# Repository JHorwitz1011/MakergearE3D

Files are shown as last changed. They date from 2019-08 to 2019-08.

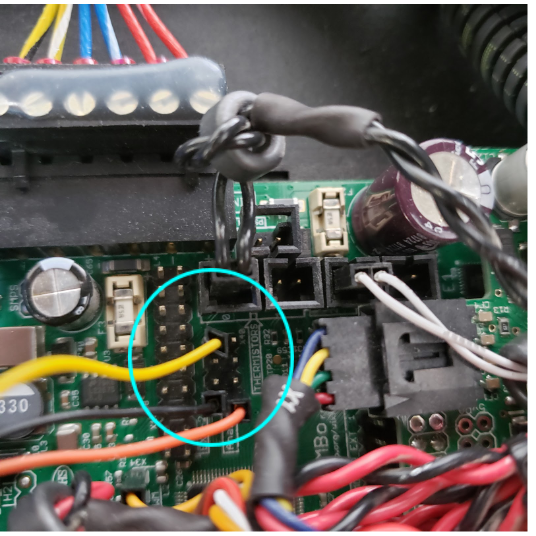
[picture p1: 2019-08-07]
Analog Pins.PNG

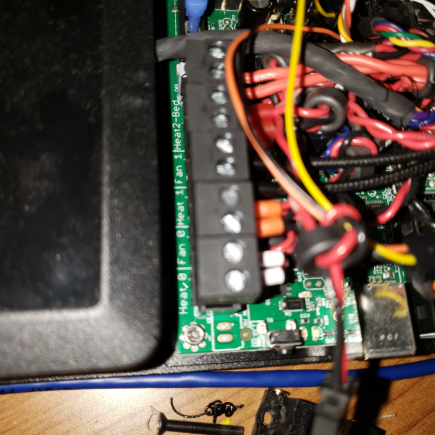
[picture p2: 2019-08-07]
Heater Pins.PNG

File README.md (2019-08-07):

# MakergearE3D

This project was creted by Jim Horwitz, an intern at MakerGear.  

Objectives  
 -- High temperature upgrade kit  
 -- E3D upgrade kit  

**Components**

Heater - https://e3d-online.com/high-temperature-heater-cartridges  
65W @ 24V  
RAMBo 1.3 MOSFETs can handle  
Rated at 117W, 89A  
Connector of heater is not compatible with the port on M3, potential mod?  
Solution: Remove the old heater block wires from the screw terminal and replace with the 65W heater wires.  
Zip tie through the back to the filament drive   

Heat Break - https://e3d-online.com/v6-titanium-heat-break-1-75mm  
Lower heat conductivity  
Maybe not necessary - requires further testing  
Alternative: https://e3d-online.com/v6-heat-break  
Plated Copper Heater Block - https://e3d-online.com/v6-plated-copper-heater-block  
Aluminum heater blocks will soften at high temperatures  

High Temp PTFE tubing - https://e3d-online.com/capricorn-bowden-tubing-100mm  
For heat sink  
Normal PTFE will melt with high temp. Materials such as PEEK  

PT100 Temperature Sensor - https://e3d-online.com/pt100-temperature-sensor  
Accurately reads temperatures up to 400 deg. C  
Alternative: https://e3d-online.com/type-k-thermocouple-cartridge  
Requires a different amplifier board  
  
PT100 Amplifier Board - https://e3d-online.com/pt100-amplifier-board  
Required for the PT100 Temperature Sensor to work  
Requires Vcc and GND pins from RAMBo 1.3  
Signal pin must be connected to analog input of RAMBo 1.3  
Explained later  

Threaded Heat Sink - https://e3d-online.com/v6-threaded-heatsink  
Alternative groove mount: https://e3d-online.com/v6-heatsink-1-75mm-universal  

**Firmware Changes** -  attached in Marlin firmware

Configuration.h

temperature sensor 1 changed to match signal from PT100 amplifier board.   

pins_RAMBO.h

temp sensor 1 pin changed to match signal pin on analog pins input.  

**Hardware Changes**

Refer to Analog pins.png

        Blue circle - Analog Pins location on RAMBo 1.3 Board

        Yellow Wire - Signal wire of PT100 Amplifier Board to corresponding analog pin 5 in firmware (shown above)
        Black Wire - GND of Amplifier Board
        Orange Wire - Vcc of Amplifier Board

Refer to Heater Pins.png 

        Heater 1 Screw Terminal - replaced with E3D Heater Cartridge wires (glossy black in the picture above)
        Third terminal from the bottom

**GCode Changes**
http://marlinfw.org/meta/gcode/  
These changes save to the EEPROM of the RAMBo board, and are not changed when updating the firmware of the board.  

Offset between nozzle - M218 command  
T1 specifies extruder head, X/Y/Z specifies axis.  
For vertical adjustments, use Z.  
-33.26 worked with an M3 with a normal T0, and a modded T1 with Ryan’s 3D printed mount  
Negative values move the bed further from the hotend (down).  

Printout from M503  

        M218 T1 X252.00 Y0.00 Z-33.26
  
http://marlinfw.org/docs/gcode/M218.html  

Autotune PID - M303  

        M303 E1 S265 C10 

This will run 10 cycles of PID autotuning based on 265 deg. C.  
Copy the PID settings into M301, using P, I, and D before each number to change their respective values.  

Printout from M503  

        M301 P15.33 I1.39 D42.38 C120.00 L20

http://marlinfw.org/docs/gcode/M303.html  
http://marlinfw.org/docs/gcode/M301.html

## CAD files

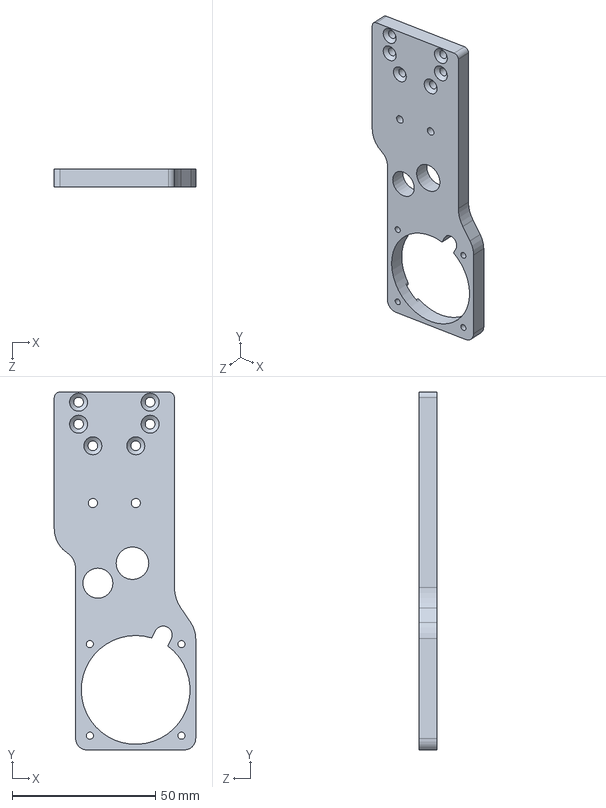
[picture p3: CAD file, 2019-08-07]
HotendMountingPlate_2516-1_REV_3.1.SLDPRT
49.5 x 125.1 x 6.35 mm

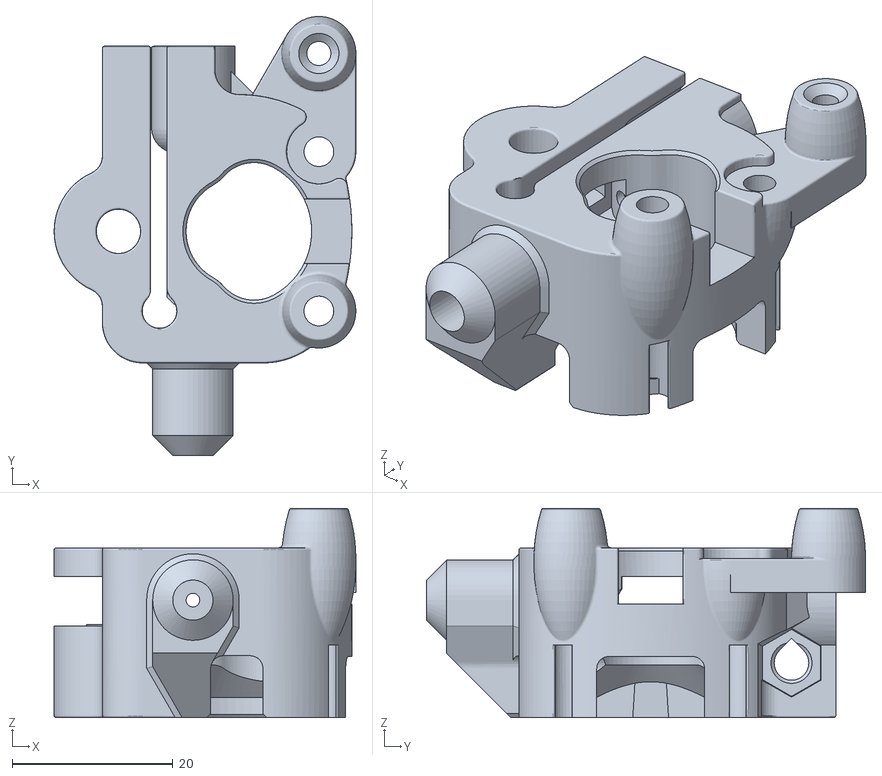
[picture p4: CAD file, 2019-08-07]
M3FilamentDrive_8-7-19 v2.stl
37.5 x 54.5 x 26.0

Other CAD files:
HotendMountingPlate_2516-1_REV_3_7-26-19 v3.step

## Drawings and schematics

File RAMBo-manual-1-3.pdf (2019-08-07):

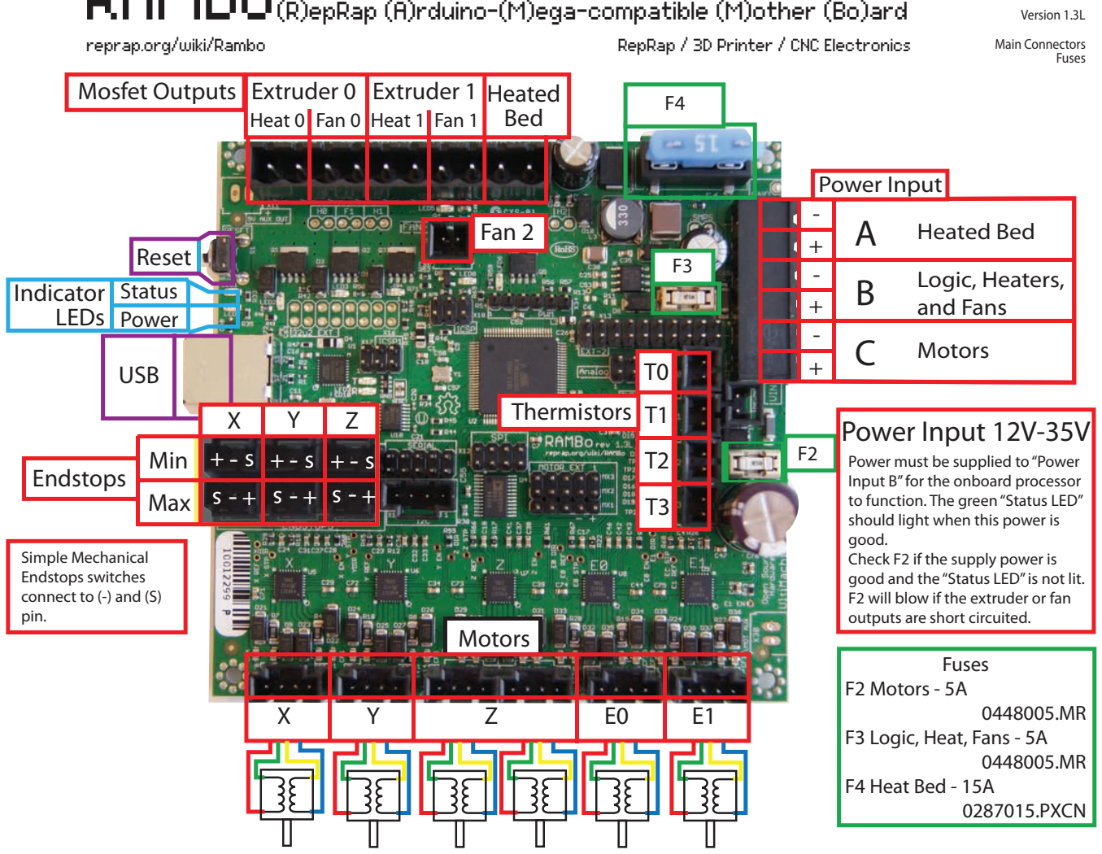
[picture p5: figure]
Fuses F2 Motors - 5A; 0448005.MR F3 Logic, Heat, Fans - 5A 0448005.MR F4 Heat Bed - 15A 0287015.PXCN; Fuses; Indicator LEDs; Status Power; Reset; USB; A Heated Bed; C Motors; Logic, Heaters, B and Fans; Power Input; Power must be supplied to “Power Input B” for the onboard processor to function. The green “Status LED” should light when this power is good. Check F2 if the supply power is good and the “Status LED” is not lit. F2 will blow if the extruder or fan outputs are short circuited.; Power Input 12V-35V; Mosfet Outputs; Extruder 0; Extruder 1; Fan 2; Heated; Heat 0; Fan 0; Heat 1; Fan 1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

Open Source Hardware | Copyright 2014 - UltiMachine -Johnny,Britt,Dorothy,Lee, Bruce

Handle with care. Static Sensitive device.

Test all electronics thoroughly before placing into service.

# Do not leave power supplied to electronics unattended, or run machines

# This is NOT a toy and it contains small and sharp parts. Children can choke or

never leave printer/parts unattended.

reprap.org/wiki/Rambo | RepRap / 3D Printer / CNC Electronics

## RAMBo(R)epRap (A)rduino-(M)ega-compatible (M)other (Bo)ard

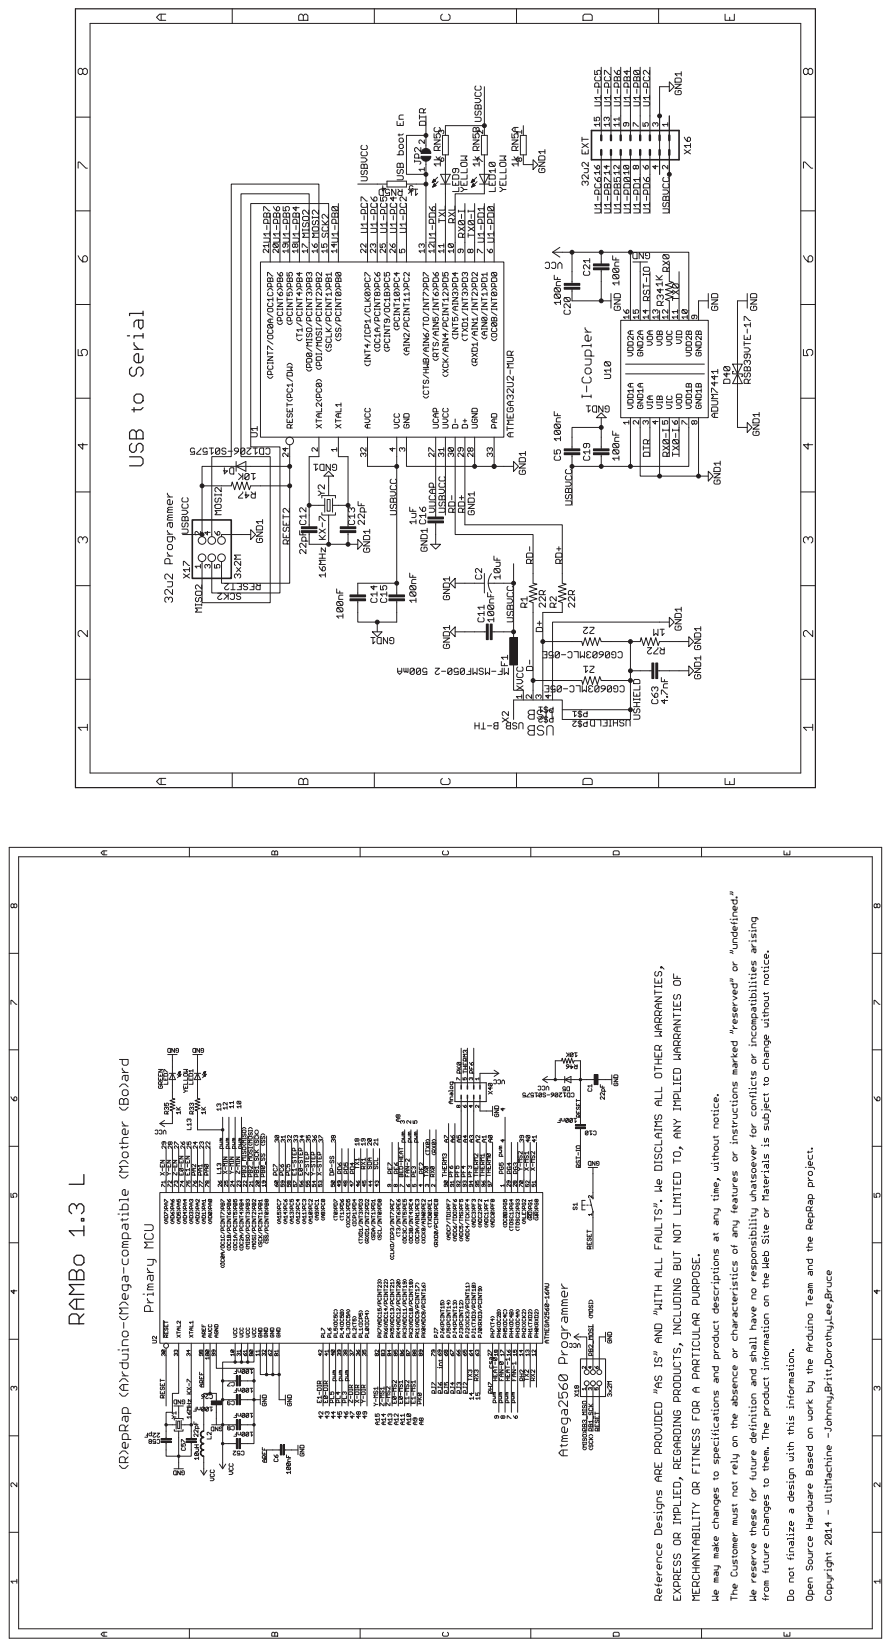
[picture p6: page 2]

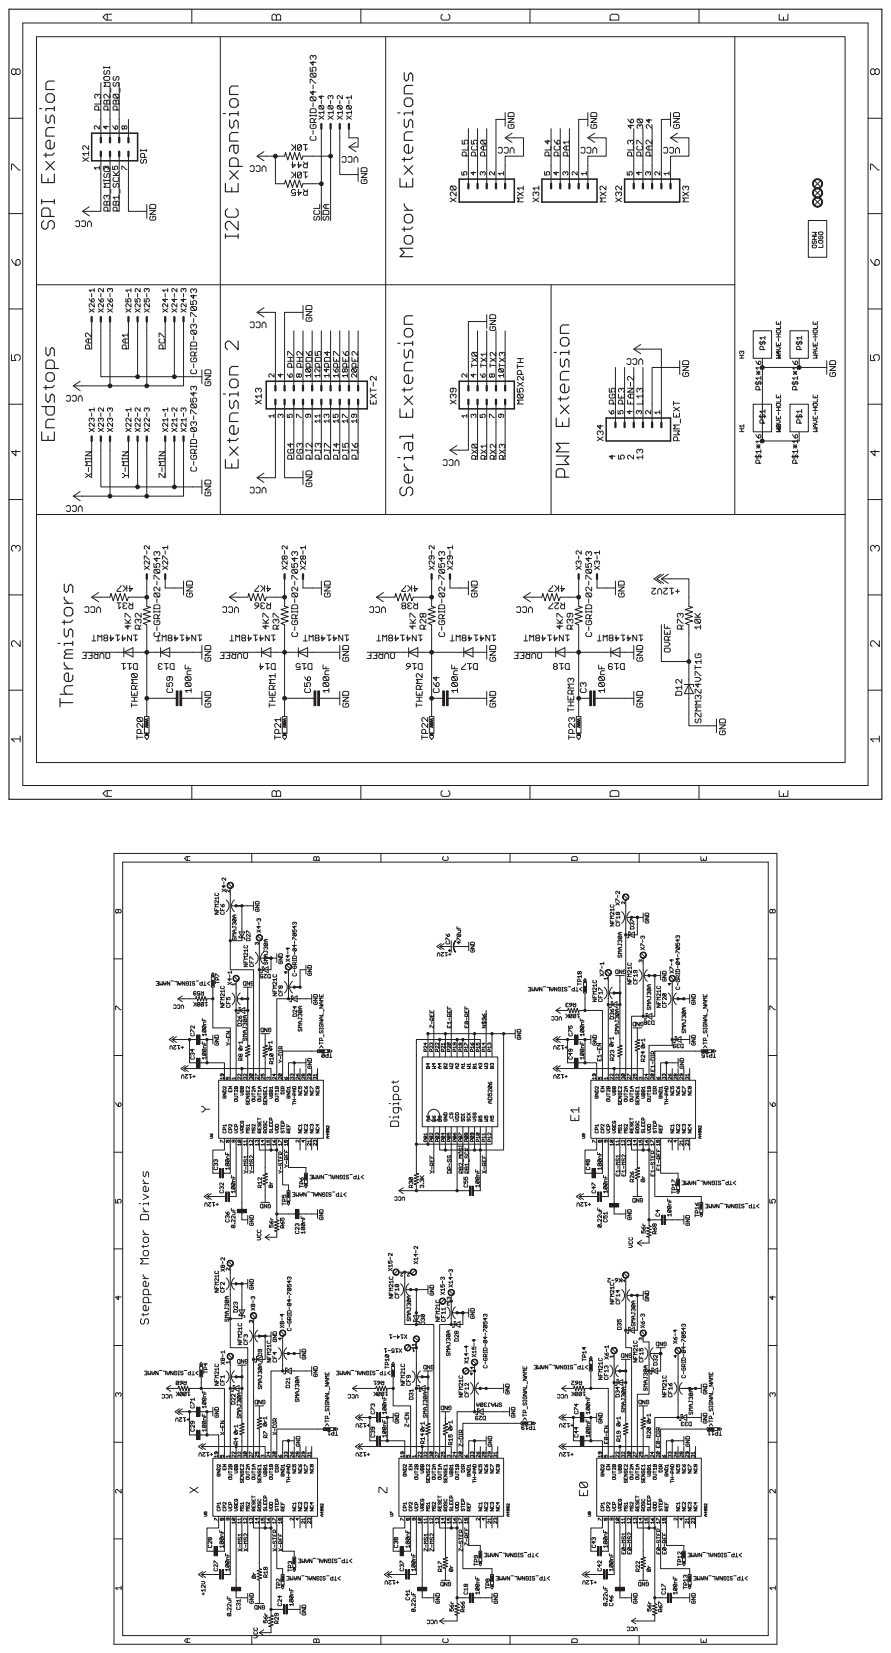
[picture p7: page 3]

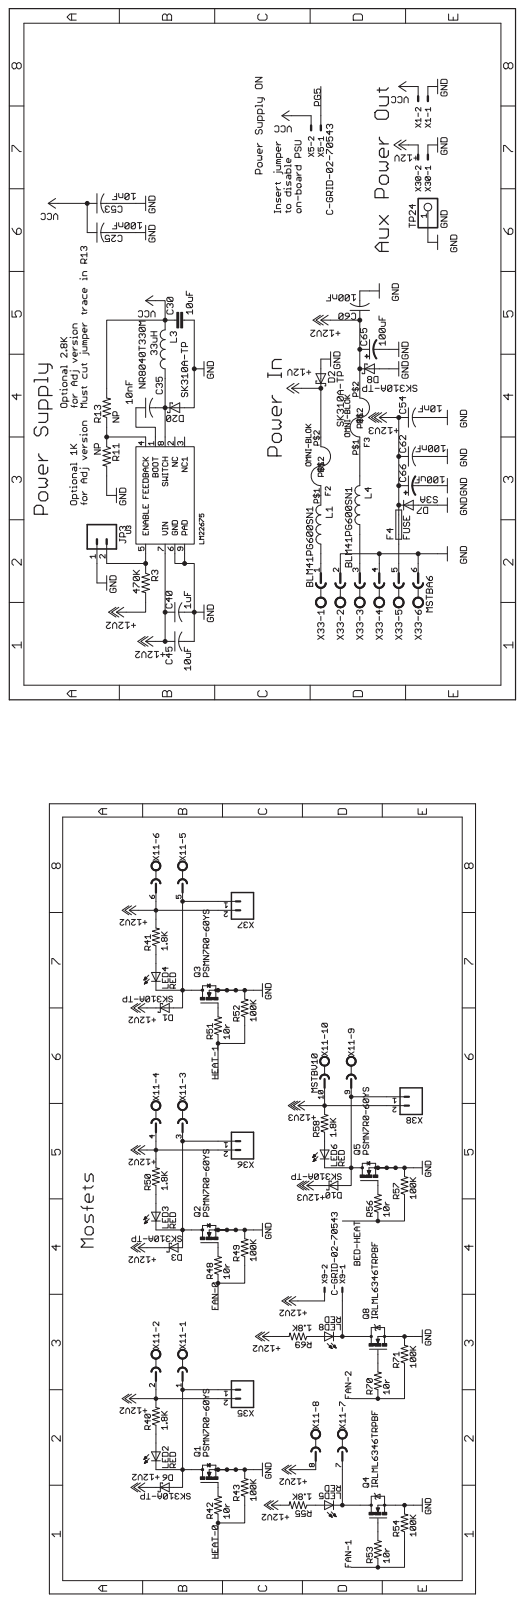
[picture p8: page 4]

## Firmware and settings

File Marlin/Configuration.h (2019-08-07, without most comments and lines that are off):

#define CONFIGURATION_H
#define CONFIGURATION_H_VERSION 010100
#define STRING_CONFIG_H_AUTHOR MAKERGEAR_AUTHOR // Who made the changes.
#define SHOW_BOOTSCREEN
#define STRING_SPLASH_LINE1 SHORT_BUILD_VERSION // will be shown during bootup in line 1
#define STRING_SPLASH_LINE2 WEBSITE_URL         // will be shown during bootup in line 2
#define SERIAL_PORT 0
#define BAUDRATE 115200
#define MOTHERBOARD BOARD_RAMBO
#define CUSTOM_MACHINE_NAME MAKERGEAR_MACHINE_NAME_STRING
#if CONF_CARRIAGE == ONE_X_CARRIAGE
#define EXTRUDERS 1
#endif
#if CONF_CARRIAGE == TWO_X_CARRIAGE
#define EXTRUDERS 2
#endif
#define HOTEND_OFFSET_X \
  {                     \
    0.0, CONF_X_T1_MAX  \
  } // (in mm) for each extruder, offset of the hotend on the X axis
#define HOTEND_OFFSET_Y \
  {                     \
    0.0, 0.00           \
  } // (in mm) for each extruder, offset of the hotend on the Y axis
#define POWER_SUPPLY 1
#define TEMP_SENSOR_0 1
#if CONF_CARRIAGE == ONE_X_CARRIAGE
#define TEMP_SENSOR_1 0
#endif
#if CONF_CARRIAGE == TWO_X_CARRIAGE
#define TEMP_SENSOR_1 20
#endif
#define TEMP_SENSOR_2 0
#define TEMP_SENSOR_3 0
#define TEMP_SENSOR_4 0
#define TEMP_SENSOR_BED 1
#define DUMMY_THERMISTOR_998_VALUE 25
#define DUMMY_THERMISTOR_999_VALUE 100
#define MAX_REDUNDANT_TEMP_SENSOR_DIFF 10
#define TEMP_RESIDENCY_TIME 2 // (seconds)
#define TEMP_HYSTERESIS 3     // (degC) range of +/- temperatures considered "close" to the target one
#define TEMP_WINDOW 4         // (degC) Window around target to start the residency timer x degC early.
#define TEMP_BED_RESIDENCY_TIME 2 // (seconds)
#define TEMP_BED_HYSTERESIS 3     // (degC) range of +/- temperatures considered "close" to the target one
#define TEMP_BED_WINDOW 2         // (degC) Window around target to start the residency timer x degC early.
#define HEATER_0_MINTEMP 5
#define HEATER_1_MINTEMP 5
#define HEATER_2_MINTEMP 5
#define HEATER_3_MINTEMP 5
#define HEATER_4_MINTEMP 5
#define BED_MINTEMP 5
#define HEATER_0_MAXTEMP 305
#define HEATER_1_MAXTEMP 305
#define HEATER_2_MAXTEMP 275
#define HEATER_3_MAXTEMP 275
#define HEATER_4_MAXTEMP 275
#define BED_MAXTEMP 150
#define PIDTEMP
#define BANG_MAX 255     // limits current to nozzle while in bang-bang mode; 255=full current
#define PID_MAX BANG_MAX // limits current to nozzle while PID is active (see PID_FUNCTIONAL_RANGE below); 255=full current
#define PID_FUNCTIONAL_RANGE 10 // If the temperature difference between the target temperature and the actual temperature \
#define K1 0.95                 //smoothing factor within the PID
#define DEFAULT_Kp CONF_HOTEND_KP
#define DEFAULT_Ki CONF_HOTEND_KI
#define DEFAULT_Kd CONF_HOTEND_KD
#define PIDTEMPBED
#define MAX_BED_POWER 255 // limits duty cycle to bed; 255=full current
#define K1_BED 0.6 //SCOTT was 0.95 //smoothing factor within the PIDwas 0.95 //smoothing factor within the PID
#define PID_BED_FUNCTIONAL_RANGE 3 //SCOTT // If the temperature difference between the target temperature and the actual temperature
#define DEFAULT_bedKp CONF_HBP_KP
#define DEFAULT_bedKi CONF_HBP_KI
#define DEFAULT_bedKd CONF_HBP_KD
#define PREVENT_COLD_EXTRUSION
#define EXTRUDE_MINTEMP 170
#define PREVENT_LENGTHY_EXTRUDE
#define EXTRUDE_MAXLENGTH 1001
#define THERMAL_PROTECTION_HOTENDS // Enable thermal protection for all extruders
#define THERMAL_PROTECTION_BED     // Enable thermal protection for the heated bed
#define USE_XMIN_PLUG
#define USE_YMIN_PLUG
#if CONF_HAS_PROBE == true
#define USE_ZMIN_PLUG //uncommented by Josh for BLTouch testing - 10/24/1017
#endif
#if CONF_CARRIAGE == TWO_X_CARRIAGE
#define USE_XMAX_PLUG
#endif
#define USE_ZMAX_PLUG
#define ENDSTOPPULLUPS // Comment this out (using // at the start of the line) to disable the endstop pullup resistors
#define X_MIN_ENDSTOP_INVERTING CONF_ENDSTOPS       // set to true to invert the logic of the endstop.
#define Y_MIN_ENDSTOP_INVERTING CONF_ENDSTOPS       // set to true to invert the logic of the endstop.
#define Z_MIN_ENDSTOP_INVERTING CONF_ENDSTOPS       // set to true to invert the logic of the endstop.
#define X_MAX_ENDSTOP_INVERTING CONF_ENDSTOPS       // set to true to invert the logic of the endstop.
#define Y_MAX_ENDSTOP_INVERTING CONF_ENDSTOPS       // set to true to invert the logic of the endstop.
#define Z_MAX_ENDSTOP_INVERTING CONF_ENDSTOPS       // set to true to invert the logic of the endstop.
#define Z_MIN_PROBE_ENDSTOP_INVERTING CONF_ENDSTOPS // set to true to invert the logic of the endstop.
#define DEFAULT_AXIS_STEPS_PER_UNIT                                                   \
  {                                                                                   \
    CONF_X_PULLEY_STEPS, CONF_Y_PULLEY_STEPS, CONF_Z_STEPS, CONF_FILAMENT_MOTOR_STEPS \
  } // default steps per unit for Makergear M2plus
#define DEFAULT_MAX_FEEDRATE                                                           \
  {                                                                                    \
    CONF_MAX_FEEDRATE_X, CONF_MAX_FEEDRATE_Y, CONF_MAX_FEEDRATE_Z, CONF_MAX_FEEDRATE_E \
  } // (mm/sec)
#define DEFAULT_MAX_ACCELERATION                                                                       \
  {                                                                                                    \
    CONF_MAX_ACCELERATION_X, CONF_MAX_ACCELERATION_Y, CONF_MAX_ACCELERATION_Z, CONF_MAX_ACCELERATION_E \
  } // X, Y, Z, E maximum start speed for accelerated moves. E default values are good for Skeinforge 40+, for older versions raise them a lot.
#define DEFAULT_ACCELERATION CONF_DEFAULT_ACCELERATION                 // X, Y, Z and E acceleration for printing moves
#define DEFAULT_RETRACT_ACCELERATION CONF_DEFAULT_RETRACT_ACCELERATION // E acceleration for retracts
#define DEFAULT_TRAVEL_ACCELERATION CONF_DEFAULT_TRAVEL_ACCELERATION   // X, Y, Z acceleration for travel (non printing) moves
#define DEFAULT_XJERK CONF_JERK_X
#define DEFAULT_YJERK CONF_JERK_Y
#define DEFAULT_ZJERK CONF_JERK_Z
#define DEFAULT_EJERK CONF_JERK_E
#define Z_MIN_PROBE_USES_Z_MIN_ENDSTOP_PIN
#if CONF_HAS_PROBE == true
#define Z_ENDSTOP_SERVO_NR 1 // Defaults to SERVO 0 connector.
#define Z_SERVO_ANGLES \
  {                    \
    10, 90             \
  } // Z Servo Deploy and Stow angles
#endif
#if CONF_HAS_PROBE == true
#define BLTOUCH //uncommented by Josh for BLTouch testing - 10/24/1017
#endif
#define PROBING_HEATERS_OFF // Turn heaters off when probing
#define PROBING_FANS_OFF    // Turn fans off when probing
#define X_PROBE_OFFSET_FROM_EXTRUDER CONF_X_PROBE_OFFSET_FROM_EXTRUDER // X offset: -left  +right  [of the nozzle] //was 0 for my version mounted in the fan, setting to 21 for David's version mounted in the cut slow
#define Y_PROBE_OFFSET_FROM_EXTRUDER CONF_Y_PROBE_OFFSET_FROM_EXTRUDER // Y offset: -front +behind [the nozzle] //was -38 for my version mounted in the fan, setting to 0 for David's version mounted in the cut slot
#define Z_PROBE_OFFSET_FROM_EXTRUDER CONF_Z_PROBE_OFFSET_FROM_EXTRUDER // Z offset: -below +above  [the nozzle]
#if CONF_HAS_PROBE == true
#define XY_PROBE_SPEED CONF_XY_PROBE_SPEED
#endif
#define Z_PROBE_SPEED_FAST HOMING_FEEDRATE_Z
#define Z_PROBE_SPEED_SLOW (Z_PROBE_SPEED_FAST / 8)
#define PROBE_DOUBLE_TOUCH
#define Z_CLEARANCE_DEPLOY_PROBE 10  // Z Clearance for Deploy/Stow
#define Z_CLEARANCE_BETWEEN_PROBES 5 // Z Clearance between probe points
#define Z_PROBE_OFFSET_RANGE_MIN -3
#define Z_PROBE_OFFSET_RANGE_MAX 0
#if CONF_HAS_PROBE == true
#define Z_MIN_PROBE_REPEATABILITY_TEST //uncommented by Josh for BLTouch testing - 10/24/1017
#endif
#define X_ENABLE_ON 0
#define Y_ENABLE_ON 0
#define Z_ENABLE_ON 0
#define E_ENABLE_ON 0 // For all extruders
#define DISABLE_X false
#define DISABLE_Y false
#define DISABLE_Z false
#define DISABLE_E false                // For all extruders
#define DISABLE_INACTIVE_EXTRUDER true // Keep only the active extruder enabled.
#define INVERT_X_DIR CONF_X_DIRECTION
#define INVERT_Y_DIR CONF_Y_DIRECTION
#define INVERT_Z_DIR CONF_Z_DIRECTION
#define INVERT_E0_DIR CONF_EXTRUDER0_DIRECTION
#define INVERT_E1_DIR CONF_EXTRUDER1_DIRECTION
#define INVERT_E2_DIR false // direction for second x motor
#define INVERT_E3_DIR true
#define INVERT_E4_DIR false
#define Z_HOMING_HEIGHT 10 // (in mm) Minimal z height before homing (G28) for Z clearance above the bed, clamps, ... \
#define X_HOME_DIR CONF_X_HOME_DIR
#define Y_HOME_DIR CONF_Y_HOME_DIR
#define Z_HOME_DIR CONF_Z_HOME_DIR
#define X_BED_SIZE CONF_X_BED_SIZE
#define Y_BED_SIZE CONF_Y_BED_SIZE
#define X_MIN_POS CONF_X_T0_MIN
#define Y_MIN_POS CONF_Y_MIN
#define Z_MIN_POS CONF_Z_MIN
#define X_MAX_POS CONF_X_T0_MAX
#define Y_MAX_POS CONF_Y_MAX
#define Z_MAX_POS CONF_Z_MAX
#define MIN_SOFTWARE_ENDSTOPS
#define MAX_SOFTWARE_ENDSTOPS
#if CONF_HAS_PROBE == true
#define AUTO_BED_LEVELING_BILINEAR //uncommented by Josh for BLTouch testing - 10/24/1017
#endif
#define DEBUG_LEVELING_FEATURE //uncommented by Josh for BLTouch testing - 10/24/1017
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

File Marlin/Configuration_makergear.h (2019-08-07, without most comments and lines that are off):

#define MAKERGEAR_MODEL_M3_ID_REV1_000//AUTOMATICALLY FILLED BY MGSETUP PLUGIN - 19-07-31.18:43
#ifdef MAKERGEAR_MODEL_M3_SINGLE_X_CARRIAGE
	#define MAKERGEAR_MODEL_M3_SE_REV0_004
#endif
#ifdef MAKERGEAR_MODEL_M3_INDEPENDENT_DUAL
	#define MAKERGEAR_MODEL_M3_ID_REV0_005
#endif
#define MAKERGEAR_AUTHOR "MG |Josh, Kyle, David, Sam"
#define M2_X_PULLEY_STEPS 88.8
#define M3_X_PULLEY_STEPS 80.1
#define M2_Y_PULLEY_STEPS 88.8
#define M3_Y_PULLEY_STEPS 80.1
#define M2_Z_STEPS 1007.7
#define M3_Z_STEPS 1007.7
#define M3_X_BED_SIZE 200
#define M3_Y_NO_PROBE_BED_SIZE 253
#define M3_Y_HAS_PROBE_BED_SIZE 233
#define M2_X_T0_MIN 0
#define M3_SE_rev_0_004_X_T0_MIN -4
#define M3_SE_rev_0_005_X_T0_MIN -4
#define M3_SE_rev_1_000_X_T0_MIN -20.77
#define M3_ID_rev_1_000_X_T0_MIN -20.77
#define M2_Y_MIN 0
#define M3_SE_rev_0_004_Y_MIN 0
#define M3_SE_rev_0_005_Y_MIN -11
#define M3_SE_rev_1_000_Y_MIN -15.5
#define M3_ID_rev_0_006_Y_MIN -11
#define M3_ID_rev_1_000_Y_MIN -15.5
#define M2_Z_MIN -15
#define M3_Z_MIN -15
#define M3_SE_rev_0_005_Z_MIN 0
#define M3_SE_rev_1_000_Z_MIN 0
#define M3_ID_rev_1_000_Z_MIN 0
#define M2_X_T0_MAX 205
#define M3_SE_rev_0_004_X_T0_MAX 220
#define M3_SE_rev_0_005_X_T0_MAX 211
#define M3_ID_X_T0_MAX 205
#define M2_Y_MAX  255
#define M3_SE_rev_0_004_Y_MAX  255
#define M3_SE_rev_0_005_Y_MAX  232
#define M3_SE_rev_1_000_Y_MAX  232
#define M3_ID_rev_1_000_Y_MAX  232
#define M2_Z_MAX 200
#define M3_Z_MAX 212
#define M3_X_T1_MIN_rev_0_000 70
#define M3_X_T1_MAX_rev_0_000 230
#define M3_X_T1_MIN_rev_0_003 48
#define M3_X_T1_MAX_rev_0_003 254
#define M3_X_T1_MIN_rev_1_003 23
#define M3_X_T1_MAX_rev_1_003 252
#define PRINTED_FILAMENT_MOTOR_CURRENT 95
#define METAL_FILAMENT_MOTOR_CURRENT 135
#define X_T0_MOTOR_CURRENT 100
#define Y_MOTOR_CURRENT 100
#define Z_MOTOR_CURRENT 190
#define E_MOTOR_CURRENT 95
#define X_T1_MOTOR_PWM 90 //daughteboard uses a different current mapping than digipot for T0
#define RAMBO_SHIELD_11 11
#define RAMBO_SHIELD_12 12
#define RAMBO_SHIELD_13 13
#define RAMBO_SHIELD_14 14
#define RAMBO_SHIELD_15 15
#define M2_PRINTED_FILAMENT_DRIVE_DIRECTION true
#define M3_PRINTED_FILAMENT_DRIVE_DIRECTION false
#define M2_X_T0_DIRECTION true
#define M3_X_T0_DIRECTION false
#define M2_Y_DIRECTION false
#define M3_Y_DIRECTION true
#define M2_Z_DIRECTION false
#define M3_Z_DIRECTION true
#define ONE_X_CARRIAGE 1
#define TWO_X_CARRIAGE 2
#define GEARBOX_FILAMENT_MOTOR_STEPS 471.5
#define DIRECT_FILAMENT_MOTOR_STEPS 88.1
#define ENDSTOPS_NC false
#define ENDSTOPS_NO true
#define AUTO_REWRITE_EEPROM	false
#define HOTEND_V5_KP 16.83
#define HOTEND_V5_KI 1.1
#define HOTEND_V5_KD 64.51
#define HBP_KP 159.7
#define HBP_KI 5.59
#define HBP_KD 1141.48
#define TOOLCHANGE_PARK_ZLIFT_DEFAULT   0.1
#define TOOLCHANGE_UNPARK_ZLIFT_DEFAULT 0.1
#define TOOLCHANGE_PARK_ZLIFT_TIGHT   0.01
#define TOOLCHANGE_UNPARK_ZLIFT_TIGHT 0.01
#define EXT_THRML_PROTECT_PERIOD_STRICT			40
#define EXT_THRML_PROTECT_HYSTERESIS_STRICT		4
#define EXT_WATCH_TEMP_PERIOD_STRICT			20
#define EXT_WATCH_TEMP_INCREASE_STRICT			2
#define BED_THRML_PROTECT_PERIOD_STRICT			120
#define BED_THRML_PROTECT_HYSTERESIS_STRICT		2
#define BED_WATCH_TEMP_PERIOD_STRICT			120
#define BED_WATCH_TEMP_INCREASE_STRICT			2
#define EXT_THRML_PROTECT_PERIOD_SAFE			45
#define EXT_THRML_PROTECT_HYSTERESIS_SAFE		10
#define EXT_WATCH_TEMP_PERIOD_SAFE				40
#define EXT_WATCH_TEMP_INCREASE_SAFE			2
#define BED_THRML_PROTECT_PERIOD_SAFE			150
#define BED_THRML_PROTECT_HYSTERESIS_SAFE		10
#define BED_WATCH_TEMP_PERIOD_SAFE				600
#define BED_WATCH_TEMP_INCREASE_SAFE			2
#define M3_MAX_FEEDRATE_X	300
#define M3_MAX_FEEDRATE_Y	300
#define M3_MAX_FEEDRATE_Z	20
#define M3_MAX_FEEDRATE_E	30
#define M3_MAX_ACCELERATION_X	1200
#define M3_MAX_ACCELERATION_Y	1200
#define M3_MAX_ACCELERATION_Z	10
#define M3_MAX_ACCELERATION_E	2000
#define M3_JERK_X	5.0
#define M3_JERK_Y	5.0
#define M3_JERK_Z	1
#define M3_JERK_E	10
#define M3_DEFAULT_ACCELERATION 		1000
#define M3_DEFAULT_RETRACT_ACCELERATION	2000
#define M3_DEFAULT_TRAVEL_ACCELERATION	1000
#define M3_HAS_PROBE	true
#define M3_NO_PROBE	false
#define M3_X_HOME_DIRECTION -1
#define M3_Y_HOME_DIRECTION -1
#define M3_Z_NO_PROBE_HOME_DIRECTION 1
#define M3_Z_HAS_PROBE_HOME_DIRECTION -1
#define MAKERGEAR_ERROR_FLAG //error flag used to detect if a model had not been choosen
#define CONF_GRID_MAX_POINTS_X 3
#define CONF_GRID_MAX_POINTS_Y CONF_GRID_MAX_POINTS_X
#define CONF_X_PROBE_OFFSET_FROM_EXTRUDER 21
#define CONF_Y_PROBE_OFFSET_FROM_EXTRUDER 0
#define CONF_Z_PROBE_OFFSET_FROM_EXTRUDER -1
#ifdef MAKERGEAR_MODEL_M2_SE_REV5_000
	#undef MAKERGEAR_ERROR_FLAG
	#define MAKERGEAR_MACHINE_NAME_STRING "M2 Single Extruder Rev 5/E"
	#define CONF_X_HOME_DIR M3_X_HOME_DIRECTION
	#define CONF_Y_HOME_DIR M3_Y_HOME_DIRECTION
	#define CONF_Z_HOME_DIR M3_Z_NO_PROBE_HOME_DIRECTION
	#define CONF_X_BED_SIZE M3_X_BED_SIZE
	#define CONF_Y_BED_SIZE 254
	#define CONF_TOOLCHANGE_PARK_ZLIFT   			TOOLCHANGE_PARK_ZLIFT_TIGHT
	#define CONF_TOOLCHANGE_UNPARK_ZLIFT 			TOOLCHANGE_UNPARK_ZLIFT_TIGHT
	#define CONF_THERMAL_PROTECTION_PERIOD 			EXT_THRML_PROTECT_PERIOD_SAFE
	#define CONF_THERMAL_PROTECTION_HYSTERESIS 		EXT_THRML_PROTECT_HYSTERESIS_SAFE
	#define CONF_WATCH_TEMP_PERIOD 					EXT_WATCH_TEMP_PERIOD_SAFE
	#define CONF_WATCH_TEMP_INCREASE 				EXT_WATCH_TEMP_INCREASE_SAFE
	#define CONF_THERMAL_PROTECTION_BED_PERIOD 		BED_THRML_PROTECT_PERIOD_SAFE
	#define CONF_THERMAL_PROTECTION_BED_HYSTERESIS 	BED_THRML_PROTECT_HYSTERESIS_SAFE
	#define CONF_WATCH_BED_TEMP_PERIOD 				BED_WATCH_TEMP_PERIOD_SAFE
	#define CONF_WATCH_BED_TEMP_INCREASE 			BED_WATCH_TEMP_INCREASE_SAFE
	#define CONF_X_PULLEY_STEPS 	M2_X_PULLEY_STEPS
	#define CONF_Y_PULLEY_STEPS 	M2_X_PULLEY_STEPS
	#define CONF_Z_STEPS			M2_Z_STEPS
	#define CONF_FILAMENT_MOTOR_STEPS  	GEARBOX_FILAMENT_MOTOR_STEPS
	#define CONF_SHIELD    			RAMBO_SHIELD_15
	#define CONF_CARRIAGE  			ONE_X_CARRIAGE
	#define CONF_ENDSTOPS  			ENDSTOPS_NO
	#define CONF_X_DIRECTION  		M2_X_T0_DIRECTION
	#define CONF_Y_DIRECTION  		M2_Y_DIRECTION
	#define CONF_Z_DIRECTION  		M2_Z_DIRECTION
	#define CONF_EXTRUDER_MOTOR_CURRENT PRINTED_FILAMENT_MOTOR_CURRENT
	#define CONF_EXTRUDER0_DIRECTION  M2_PRINTED_FILAMENT_DRIVE_DIRECTION
	#define CONF_EXTRUDER1_DIRECTION  M2_PRINTED_FILAMENT_DRIVE_DIRECTION
	#define CONF_X_T0_MAX 			M2_X_T0_MAX
	#define CONF_Y_MAX 				M2_Y_MAX
	#define CONF_Z_MAX 				M2_Z_MAX
	#define CONF_X_T0_MIN 			M2_X_T0_MIN
	#define CONF_Y_MIN 				M2_Y_MIN
	#define CONF_Z_MIN 				M2_Z_MIN
	#define CONF_HOTEND_KP HOTEND_V5_KP
	#define CONF_HOTEND_KI HOTEND_V5_KI
	#define CONF_HOTEND_KD HOTEND_V5_KD
	#define CONF_HBP_KP HBP_KP
	#define CONF_HBP_KI HBP_KI
	#define CONF_HBP_KD HBP_KD
	#define CONF_THERMAL_PROTECTION_PERIOD 			EXT_THRML_PROTECT_PERIOD_SAFE
	#define CONF_THERMAL_PROTECTION_HYSTERESIS 		EXT_THRML_PROTECT_HYSTERESIS_SAFE
	#define CONF_WATCH_TEMP_PERIOD 					EXT_WATCH_TEMP_PERIOD_SAFE
	#define CONF_WATCH_TEMP_INCREASE 				EXT_WATCH_TEMP_INCREASE_SAFE
	#define CONF_THERMAL_PROTECTION_BED_PERIOD 		BED_THRML_PROTECT_PERIOD_SAFE
	#define CONF_THERMAL_PROTECTION_BED_HYSTERESIS 	BED_THRML_PROTECT_HYSTERESIS_SAFE
	#define CONF_WATCH_BED_TEMP_PERIOD 				BED_WATCH_TEMP_PERIOD_SAFE
	#define CONF_WATCH_BED_TEMP_INCREASE 			BED_WATCH_TEMP_INCREASE_SAFE
	#define CONF_MAX_FEEDRATE_X 	M3_MAX_FEEDRATE_X
	#define CONF_MAX_FEEDRATE_Y		M3_MAX_FEEDRATE_Y
	#define CONF_MAX_FEEDRATE_Z		M3_MAX_FEEDRATE_Z
	#define CONF_MAX_FEEDRATE_E		M3_MAX_FEEDRATE_E
	#define CONF_MAX_ACCELERATION_X		M3_MAX_ACCELERATION_X
	#define CONF_MAX_ACCELERATION_Y		M3_MAX_ACCELERATION_Y
	#define CONF_MAX_ACCELERATION_Z		M3_MAX_ACCELERATION_Z
	#define CONF_MAX_ACCELERATION_E		M3_MAX_ACCELERATION_E
	#define CONF_JERK_X		M3_JERK_X
	#define CONF_JERK_Y		M3_JERK_Y
	#define CONF_JERK_Z		M3_JERK_Z
	#define CONF_JERK_E		M3_JERK_E
	#define CONF_DEFAULT_ACCELERATION 			M3_DEFAULT_ACCELERATION
	#define CONF_DEFAULT_RETRACT_ACCELERATION	M3_DEFAULT_RETRACT_ACCELERATION
	#define CONF_DEFAULT_TRAVEL_ACCELERATION	M3_DEFAULT_TRAVEL_ACCELERATION
	#define CONF_HAS_PROBE M3_NO_PROBE
	#define SDSUPPORT
#endif
#ifdef MAKERGEAR_MODEL_M3_SE_REV0_004
	#undef MAKERGEAR_ERROR_FLAG
	#define MAKERGEAR_MACHINE_NAME_STRING "M3 Single Extruder Rev 0_004"
	#define CONF_X_HOME_DIR M3_X_HOME_DIRECTION
	#define CONF_Y_HOME_DIR M3_Y_HOME_DIRECTION
	#define CONF_Z_HOME_DIR M3_Z_NO_PROBE_HOME_DIRECTION
	#define CONF_X_BED_SIZE M3_X_BED_SIZE
	#define CONF_Y_BED_SIZE 254
	#define CONF_TOOLCHANGE_PARK_ZLIFT   			TOOLCHANGE_PARK_ZLIFT_TIGHT
	#define CONF_TOOLCHANGE_UNPARK_ZLIFT 			TOOLCHANGE_UNPARK_ZLIFT_TIGHT
	#define CONF_THERMAL_PROTECTION_PERIOD 			EXT_THRML_PROTECT_PERIOD_SAFE
	#define CONF_THERMAL_PROTECTION_HYSTERESIS 		EXT_THRML_PROTECT_HYSTERESIS_SAFE
	#define CONF_WATCH_TEMP_PERIOD 					EXT_WATCH_TEMP_PERIOD_SAFE
	#define CONF_WATCH_TEMP_INCREASE 				EXT_WATCH_TEMP_INCREASE_SAFE
	#define CONF_THERMAL_PROTECTION_BED_PERIOD 		BED_THRML_PROTECT_PERIOD_SAFE
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

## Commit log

2019-08-07 Create M3FilamentDrive_8-7-19 v2.step
    [M3FilamentDrive_8-7-19 v2.step]
2019-08-07 updated models
    [HotendMountingPlate_2516-1_REV_3_7-26-19 v3.step, M3FilamentDrive_8-7-19 v2.step, M3FilamentDrive_8-7-19 v2.stl]
2019-08-07 added solidworks part
    [HotendMountingPlate_2516-1_REV_3.1.SLDPRT]

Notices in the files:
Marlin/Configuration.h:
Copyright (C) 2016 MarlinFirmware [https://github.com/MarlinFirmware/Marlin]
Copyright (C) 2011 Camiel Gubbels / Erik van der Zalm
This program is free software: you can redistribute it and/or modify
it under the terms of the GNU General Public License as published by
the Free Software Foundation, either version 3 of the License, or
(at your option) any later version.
